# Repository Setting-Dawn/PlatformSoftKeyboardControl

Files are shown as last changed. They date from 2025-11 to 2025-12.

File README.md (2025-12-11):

#  PlatformSoftKeyboardControl 
Control a 2 Degree of Freedom Platform using a soft sensing sheet.

This README is also used as the main page for the Doxygen-generated documentation.
The remainder of this file contains project details, diagrams, and usage
information.
# PlatformSoftKeyboardControl 

Project Goal:

Control a 2 Degree of Freedom Platform using a custom piezoresistive sensing sheet.
## Mechanical Considerations
The balancing table is controlled by two motors connected to the table's surface via a strut with two ball joints that control rotation about perpendicular axes.

Lever Arm Powered By Motor

## Software Design
### Task Diagram

ESP32 Code Task Diagram

### Webserver Task 
The ESP32 hosts its own wifi on which it hosts a webpage on 192.168.5.1 that communicates the recorded data in csv forma to either the user or an external program that interprets it. The functionality of this task is based on an example by A. Sinha.

Webserver Task State Diagram

### Motor Control Task 
The motor control task awaits confirmation that the IMU has initialized and then begins operating the motor PIDs according to the setpoint stored in the xBar and yBar shares.

Motor Control State Diagram

### Material Reading Task 
In order to perform EIT analysis, a series of voltage differences needs to be measured. For one complete measurement, one electrode is grounded while its neighboring electrode is supplied with a current while the remaining electrodes are used to measure the voltage differences. This is then repeated for each electrode. This task is responsible for taking those individual datapoints and reporting the resulting 208 values to the webpage task to be published in csv format.

Material Reading State Diagram

### PyEIT interpretation
A python script using the pyEIT module is able to read the data hosted by the webpage and analyze any changes in resistivity of the material. The resulting centroid is then passed back to the webpage using url arguments.

## Other Code Used
- Liu, et al:
+ - https://github.com/eitcom/pyEIT 
- bryanduxbury:
+ - https://github.com/bryanduxbury/adc128d818_driver 
- yuskegoto:
+ - https://github.com/yuskegoto/PCA9956 
- spluttflob:
+ - PrintStream Library https://github.com/spluttflob/Arduino-PrintStream.git 
+ - ME507 Support Library https://github.com/spluttflob/ME507-Support.git
- madhephaestus:
+ - https://github.com/madhephaestus/ESP32Encoder

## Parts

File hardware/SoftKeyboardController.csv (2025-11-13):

Reference | Qty | Value | DNP | Exclude from BOM | Exclude from Board | Footprint | Datasheet
C1 | 1 | 470μF |  |  |  | Capacitor_THT:CP_Radial_D10.0mm_P5.00mm | ~
C2,C4,C5 | 3 | 0.1μF |  |  |  | Capacitor_SMD:C_0805_2012Metric | ~
C3 | 1 | 10μF |  |  |  | Capacitor_SMD:C_0805_2012Metric | ~
C6 | 1 | 2.2μF |  |  |  | Capacitor_SMD:C_0805_2012Metric | ~
ESP1 | 1 | NodeMCU |  |  |  | ME507F24:ESP32_NodeMCU_KeeYees
H1,H2,H3,H4 | 4 | MountingHole |  | Excluded from BOM |  | MountingHole:MountingHole_2.5mm | ~
IC1 | 1 | PCA9956BTWY |  |  |  | SOP50P640X110-39N | http://www.nxp.com/docs/en/data-sheet/PCA9956B.pdf
J1 | 1 | Barrel_Jack_Switch |  |  |  | Connector_BarrelJack:BarrelJack_CUI_PJ-102AH_Horizontal | ~
J2 | 1 | EXT IMU Connection |  |  |  | Connector_PinHeader_2.54mm:PinHeader_1x05_P2.54mm_Vertical | ~
J3 | 1 | Motor 1 |  |  |  | TerminalBlock_Phoenix:TerminalBlock_Phoenix_MKDS-1,5-2_1x02_P5.00mm_Horizontal | ~
J4 | 1 | Motor 2 |  |  |  | TerminalBlock_Phoenix:TerminalBlock_Phoenix_MKDS-1,5-2_1x02_P5.00mm_Horizontal | ~
J5,J6 | 2 | Conn_01x12_Socket |  |  |  | Connector_PinSocket_2.54mm:PinSocket_1x12_P2.54mm_Vertical | ~
J7,J8 | 2 | Conn_01x08_Socket |  |  |  | Connector_PinSocket_2.54mm:PinSocket_1x08_P2.54mm_Vertical | ~
J9 | 1 | Motor Encoder 2 |  |  |  | Connector_Molex:Molex_KK-396_A-41792-0005_1x05_P3.96mm_Horizontal | ~
J10 | 1 | Motor Encoder 1 |  |  |  | Connector_Molex:Molex_KK-396_A-41792-0005_1x05_P3.96mm_Horizontal | ~
R1,R5,R13 | 3 | 10kΩ |  |  |  | Resistor_SMD:R_0805_2012Metric | ~
R2,R6 | 2 | 4.7kΩ |  |  |  | Resistor_SMD:R_0805_2012Metric | ~
R3,R4 | 2 | 500mΩ |  |  |  | Resistor_SMD:R_0805_2012Metric | ~
R7 | 1 | 3.3kΩ |  |  |  | Resistor_SMD:R_0805_2012Metric | ~
R8,R9,R10,R11 | 4 | 470Ω |  |  |  | Resistor_SMD:R_0805_2012Metric | ~
R12 | 1 | 100 |  |  |  | Resistor_SMD:R_0805_2012Metric | ~
R14 | 1 | 1kΩ |  |  |  | Resistor_SMD:R_0805_2012Metric | ~
TP1,TP2,TP3,TP4,TP5,TP6,TP7,TP8,TP9,TP10,TP11 | 11 | TestPoint |  |  |  | TestPoint:TestPoint_Loop_D1.80mm_Drill1.0mm_Beaded | ~
U2,U3 | 2 | ADC128D818 |  |  |  | Package_SO:TSSOP-16_4.4x5mm_P0.65mm | http://www.ti.com/lit/ds/symlink/adc128d818.pdf
U4 | 1 | TL071 |  |  |  | Package_TO_SOT_SMD:SOT-23-5 | http://www.ti.com/lit/ds/symlink/tl071.pdf
U5 | 1 | CD74HC4067SM |  |  |  | Package_SO:SSOP-24_5.3x8.2mm_P0.65mm | http://www.ti.com/lit/ds/symlink/cd74hc4067.pdf
U6 | 1 | DRV8848 |  |  |  | Package_SO:TSSOP-16-1EP_4.4x5mm_P0.65mm | http://www.ti.com/lit/ds/symlink/drv8848.pdf

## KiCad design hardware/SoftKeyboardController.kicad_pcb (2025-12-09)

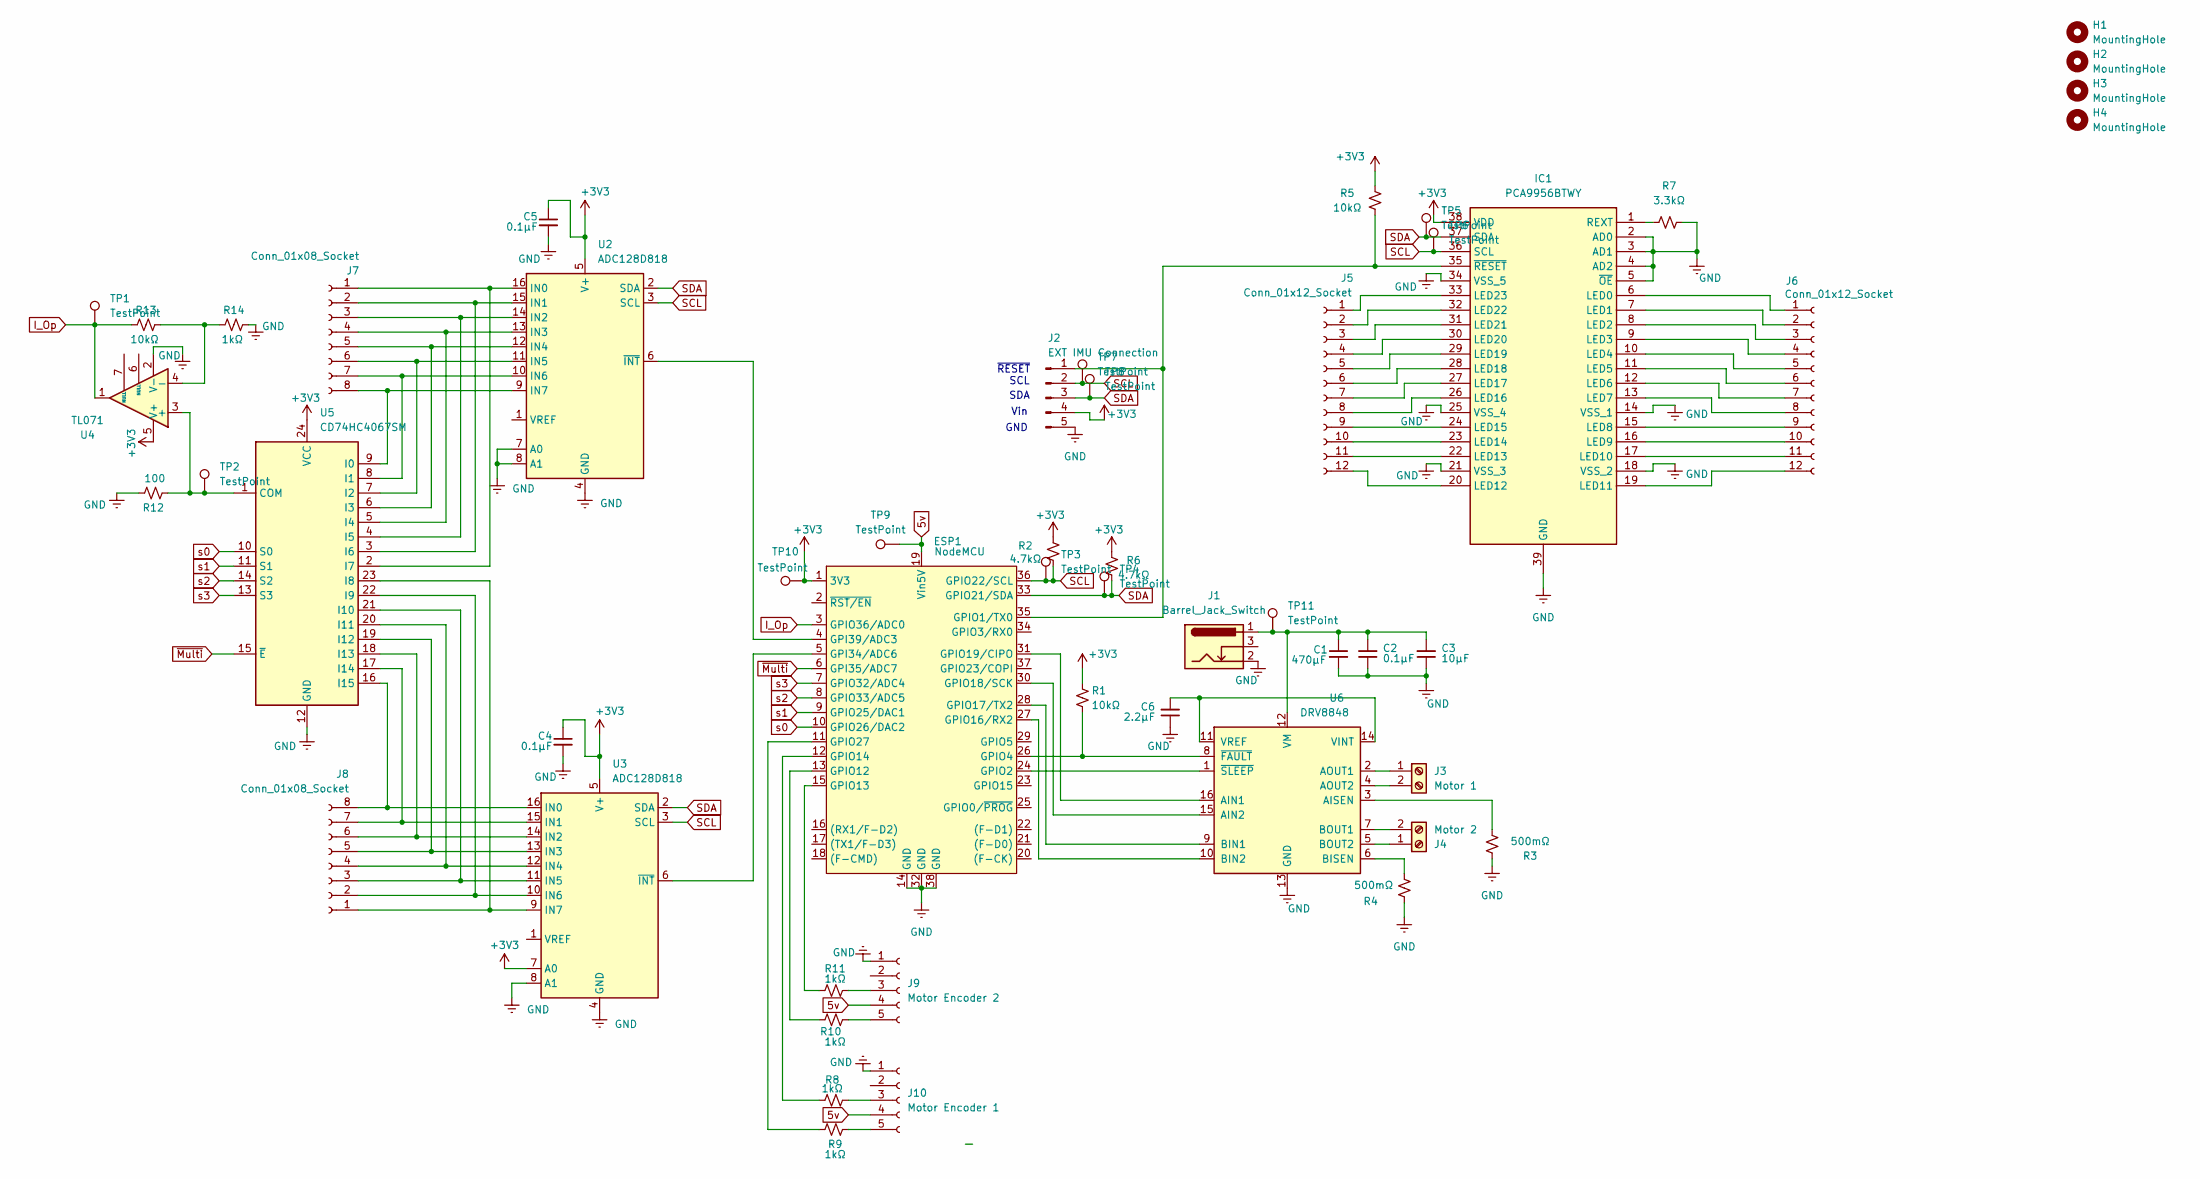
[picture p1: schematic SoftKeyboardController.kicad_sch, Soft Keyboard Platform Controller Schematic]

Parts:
C1: 470μF; CP_Radial_D10.0mm_P5.00mm
C2, C4, C5: 0.1μF; C_0805_2012Metric
C3: 10μF; C_0805_2012Metric
C6: 2.2μF; C_0805_2012Metric
ESP1: NodeMCU; ESP32_NodeMCU_KeeYees
H1, H2, H3, H4: MountingHole; MountingHole_2.5mm
IC1: PCA9956BTWY; SOP50P640X110-39N; Manufacturer_Part_Number PCA9956BTWY; Mouser Part Number 771-PCA9956BTWY
J1: Barrel_Jack_Switch; BarrelJack_CUI_PJ-102AH_Horizontal
J2: EXT IMU Connection; PinHeader_1x05_P2.54mm_Vertical
J3: Motor 1; TerminalBlock_Phoenix_MKDS-1,5-2_1x02_P5.00mm_Horizontal
J4: Motor 2; TerminalBlock_Phoenix_MKDS-1,5-2_1x02_P5.00mm_Horizontal
J5, J6: Conn_01x12_Socket; PinSocket_1x12_P2.54mm_Vertical
J7, J8: Conn_01x08_Socket; PinSocket_1x08_P2.54mm_Vertical
J9: Motor Encoder 2; Molex_KK-396_A-41792-0005_1x05_P3.96mm_Horizontal
J10: Motor Encoder 1; Molex_KK-396_A-41792-0005_1x05_P3.96mm_Horizontal
R1, R5, R13: 10kΩ; R_0805_2012Metric
R2, R6: 4.7kΩ; R_0805_2012Metric
R3, R4: 500mΩ; R_0805_2012Metric
R7: 3.3kΩ; R_0805_2012Metric
R8, R9, R10, R11, R14: 1kΩ; R_0805_2012Metric
R12: 100; R_0805_2012Metric
TP1, TP2, TP3, TP4, TP5, TP6, TP7, TP8, TP9, TP10, TP11: TestPoint; TestPoint_Loop_D1.80mm_Drill1.0mm_Beaded
U2, U3: ADC128D818; TSSOP-16_4.4x5mm_P0.65mm
U4: TL071; SOT-23-5
U5: CD74HC4067SM; SSOP-24_5.3x8.2mm_P0.65mm
U6: DRV8848; TSSOP-16-1EP_4.4x5mm_P0.65mm

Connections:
5v: ESP1.19 (Vin5V), J9.4, J10.4, TP9.1
+3V3: C4.1, C5.1, ESP1.1 (3V3), IC1.38 (VDD), J2.4, R1.1, R2.1, R5.1, R6.1, TP10.1, U2.5 (V+), U3.5 (V+), U3.7 (A0), U4.5 (V+), U5.24 (VCC)
GND: C1.2, C2.1, C3.1, C4.2, C5.2, C6.1, ESP1.14 (GND), ESP1.32 (GND), ESP1.38 (GND), IC1.2 (AD0), IC1.3 (AD1), IC1.4 (AD2), IC1.5 (~OE), IC1.14 (VSS_1), IC1.18 (VSS_2), IC1.21 (VSS_3), IC1.25 (VSS_4), IC1.34 (VSS_5), IC1.39 (GND), J1.2, J2.5, J9.1, J10.1, R3.1, R4.1, R7.1, R12.1, R14.1, U2.4 (GND), U2.7 (A0), U2.8 (A1), U3.4 (GND), U3.8 (A1), U4.2 (V-), U5.12 (GND), U6.13 (GND), U6.17 (GND)
I_Op: ESP1.3 (GPIO36/ADC0), R13.2, TP1.1, U4.1
unnamed: ESP1.5 (GPI34/ADC6), U3.6 (~INT)
unnamed: ESP1.4 (GPI39/ADC3), U2.6 (~INT)
unnamed: ESP1.35 (GPIO1/TX0), IC1.35 (~RESET), J2.1, R5.2
unnamed: ESP1.24 (GPIO2), U6.1 (~SLEEP)
unnamed: ESP1.26 (GPIO4), R1.2, U6.8 (~FAULT)
unnamed: ESP1.13 (GPIO12), R10.1
unnamed: ESP1.15 (GPIO13), R11.1
unnamed: ESP1.12 (GPIO14), R8.1
unnamed: ESP1.27 (GPIO16/RX2), U6.10 (BIN2)
unnamed: ESP1.28 (GPIO17/TX2), U6.9 (BIN1)
unnamed: ESP1.30 (GPIO18/SCK), U6.15 (AIN2)
unnamed: ESP1.31 (GPIO19/CIPO), U6.16 (AIN1)
unnamed: ESP1.11 (GPIO27), R9.1
unnamed: IC1.6 (LED0), J6.1
unnamed: IC1.7 (LED1), J6.2
unnamed: IC1.8 (LED2), J6.3
unnamed: IC1.9 (LED3), J6.4
unnamed: IC1.10 (LED4), J6.5
unnamed: IC1.11 (LED5), J6.6
unnamed: IC1.12 (LED6), J6.7
unnamed: IC1.13 (LED7), J6.8
unnamed: IC1.15 (LED8), J6.9
unnamed: IC1.16 (LED9), J6.10
unnamed: IC1.17 (LED10), J6.11
unnamed: IC1.19 (LED11), J6.12
unnamed: IC1.20 (LED12), J5.12
unnamed: IC1.22 (LED13), J5.11
unnamed: IC1.23 (LED14), J5.10
unnamed: IC1.24 (LED15), J5.9
unnamed: IC1.26 (LED16), J5.8
unnamed: IC1.27 (LED17), J5.7
unnamed: IC1.28 (LED18), J5.6
unnamed: IC1.29 (LED19), J5.5
unnamed: IC1.30 (LED20), J5.4
unnamed: IC1.31 (LED21), J5.3
unnamed: IC1.32 (LED22), J5.2
unnamed: IC1.33 (LED23), J5.1
unnamed: IC1.1 (REXT), R7.2
unnamed: J3.1, U6.2 (AOUT1)
unnamed: J3.2, U6.4 (AOUT2)
unnamed: J4.1, U6.5 (BOUT2)
unnamed: J4.2, U6.7 (BOUT1)
unnamed: J7.1, U2.16 (IN0), U5.2 (I7)
unnamed: J7.2, U2.15 (IN1), U5.3 (I6)
unnamed: J7.3, U2.14 (IN2), U5.4 (I5)
unnamed: J7.4, U2.13 (IN3), U5.5 (I4)
unnamed: J7.5, U2.12 (IN4), U5.6 (I3)
unnamed: J7.6, U2.11 (IN5), U5.7 (I2)
unnamed: J7.7, U2.10 (IN6), U5.8 (I1)
unnamed: J7.8, U2.9 (IN7), U5.9 (I0)
unnamed: J8.1, U3.9 (IN7), U5.23 (I8)
unnamed: J8.2, U3.10 (IN6), U5.22 (I9)
unnamed: J8.3, U3.11 (IN5), U5.21 (I10)
unnamed: J8.4, U3.12 (IN4), U5.20 (I11)
unnamed: J8.5, U3.13 (IN3), U5.19 (I12)
unnamed: J8.6, U3.14 (IN2), U5.18 (I13)
unnamed: J8.7, U3.15 (IN1), U5.17 (I14)
unnamed: J8.8, U3.16 (IN0), U5.16 (I15)
unnamed: J9.3, R11.2
unnamed: J9.5, R10.2
unnamed: J10.3, R8.2
unnamed: J10.5, R9.2
unnamed: R12.2, TP2.1, U4.3 (+), U5.1 (COM)
unnamed: R13.1, R14.2, U4.4 (-)
unnamed: R3.2, U6.3 (AISEN)
unnamed: R4.2, U6.6 (BISEN)
unnamed: C6.2, U6.11 (VREF), U6.14 (VINT)
unnamed: C1.1, C2.2, C3.2, J1.1, TP11.1, U6.12 (VM)
SCL: ESP1.36 (GPIO22/SCL), IC1.36 (SCL), J2.2, R2.2, TP3.1, TP6.1, TP7.1, U2.3 (SCL), U3.3 (SCL)
SDA: ESP1.33 (GPIO21/SDA), IC1.37 (SDA), J2.3, R6.2, TP4.1, TP5.1, TP8.1, U2.2 (SDA), U3.2 (SDA)
s0: ESP1.10 (GPIO26/DAC2), U5.10 (S0)
s1: ESP1.9 (GPIO25/DAC1), U5.11 (S1)
s2: ESP1.8 (GPIO33/ADC5), U5.14 (S2)
s3: ESP1.7 (GPIO32/ADC4), U5.13 (S3)
~Multi: ESP1.6 (GPI35/ADC7), U5.15 (~E)

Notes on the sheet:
GND
~{RESET}
Vin
SDA
SCL

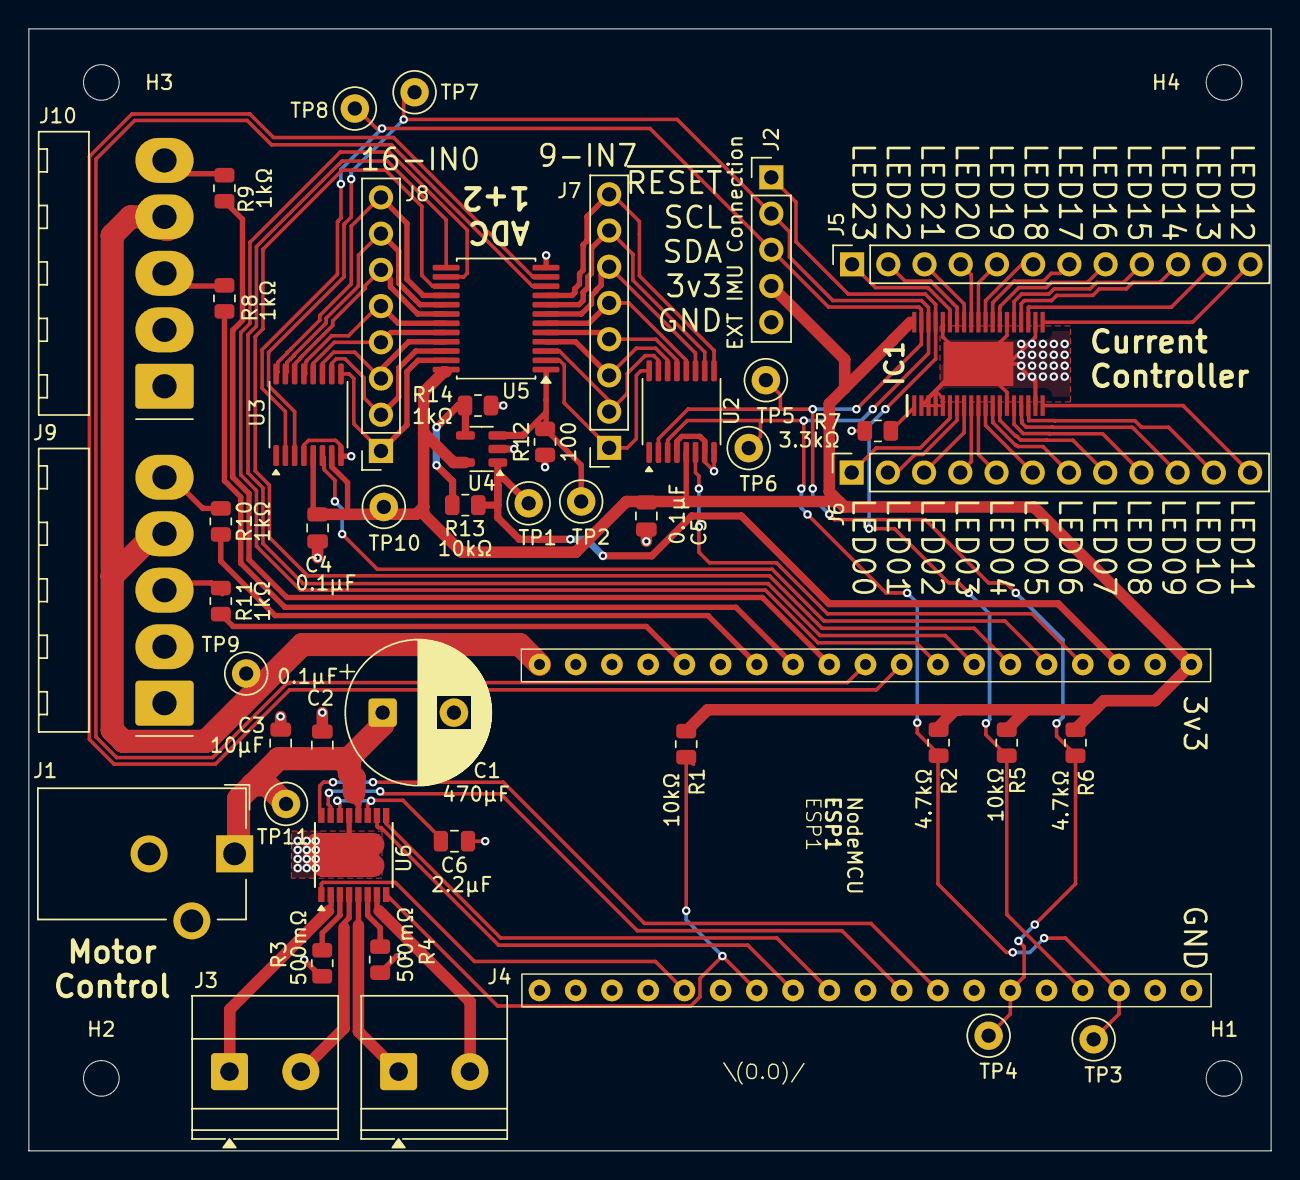
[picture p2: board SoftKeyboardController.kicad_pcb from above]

Board: 2 copper layers, 87.1 x 78.7 mm, 52 parts (0 on the bottom side), 79 nets.

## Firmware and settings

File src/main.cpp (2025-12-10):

/*! @file main.cpp
*   @brief This project was created to run the soft-sensor activated balancing platform
*   as the final project of Cal Poly SLO Fall ME 507 class.
*   @author Setting-Dawn
*   @author Jake Rowen
*   @author Ethan Siahpush
*   @version 2.0.0
*   @date 2025-Dec-09
*/

#include <Arduino.h>
#include <ESP32Encoder.h>
#include <Wire.h>
#include <Adafruit_Sensor.h>
#include <Adafruit_BNO055.h>
#include <cmath>
#include <WebServer.h>

#include "ADC128D818.h"
#include "PCA9956.h"
#include "PrintStream.h"

#include "IMU.h"
#include "MOTOR.h"
#include "ENCODER.h"
#include "EITwebhost.h"
#include "CD74HC4067SM.h"
#include "shares.h"

#undef DEBUG_MOTOR
#undef DEBUG_READMATERIAL
#undef DEBUG_ALL
#undef DEBUG_WEB
#undef SCANTWI

#ifdef DEBUG_ALL
#define DEBUG_MOTOR
#define DEBUG_READMATERIAL
#define DEBUG_WEB
#endif

// Multiplexer control pins
const uint8_t s0_PIN = 26;
const uint8_t s1_PIN = 25;
const uint8_t s2_PIN = 33;
const uint8_t s3_PIN = 32;
const uint8_t MultiEnable_PIN = 35;

// ADC TWI Addresses
const uint8_t ADC_1ADDRESS = 0x1D;
const uint8_t ADC_2ADDRESS = 0x1F;

// PCA9956BTWY Address
const uint8_t PCA9956_ADDRESS = 0x01;
PCA9956 CurrCtrl (&Wire);

// Pin definition for motors
uint8_t nSleepPin = 02;

uint8_t motorXPin1 = 19;
uint8_t motorXPin2 = 18;

uint8_t motorYPin1 = 17;
uint8_t motorYPin2 = 16;
ESP32Encoder encoderX;
ESP32Encoder encoderY;

// A share which holds whether the external program needs to initialize
Share<bool> initializeVFLG ("Measure V0");
// A share which holds whether the external program should read voltages
Share<bool> readVFLG ("Read V");
// Shares to communicate target position between webpage and motor control tasks
Share<float> xBar ("X Centroid");
Share<float> yBar ("Y Centroid");
// A share which holds the data to be published
float publish[208] = {0};
Share<bool> dataAvailable ("Publish Flag");
// Mutex to thread protect the
SemaphoreHandle_t twiMutex;

/*!
* @brief Task to handle cycling through the pins to take EIT voltage readings
* @details First waits for initialization of twi communication to complete.
* Then each round has one channel with an applied current, one grounded, and 14 others.
* ADCs read all adc channels, discards the two non-read channels, finds the deltaV between appropriate pins
* and stores all values in the resulting array into a global array after lowering the dataAvailable flag.
* @param p_params void*, unused.
*/
void task_ReadMaterial(void* p_params) {
    Serial << "Starting Read Material Task" << endl;
    ADC128D818 ADC_1 (ADC_1ADDRESS);
    ADC128D818 ADC_2 (ADC_2ADDRESS);
    CD74HC4067SM Multiplex (s0_PIN,s1_PIN,s2_PIN,s3_PIN,MultiEnable_PIN);
    PCA9956 CurrCtrl (&Wire);

    const uint8_t maxCurrent = 0xFF;

    uint8_t currPinIndex;
    double measure[208] = {0}; // Somewhere to store the data for 1 complete measurement
    double cycleVals[16]; // Somewhere to store the data for 1 energization state
    double skipCycleVals[14]; // Somewhere to store the important data begining at the correct index for 1 energization state
    Serial << "Finished initializing Read Material Task" << endl;

    uint8_t cycleIndex = 0;
    uint8_t state = 0; // Initialization State

    for (;;) {
        #ifdef DEBUG_READMATERIAL
        Serial << "Material Task " << state << endl;
        #endif
        // Operation requires the TWI devices be initialized, but other tasks include other twi devices.
        // Priority for this isn't important, so it will just sit in this state until able to initialize.
        if (state == 0) // Start TWI communication
        {
            if (xSemaphoreTake(twiMutex,5) == pdTRUE) // Takes the mutex and returns true if successful
            {
                ADC_1.setOperationMode(SINGLE_ENDED); //Mode 1 reads voltages on channels 0-7
                ADC_1.begin(); // Initializes ADC1
                ADC_2.setOperationMode(SINGLE_ENDED);//Mode 1 reads voltages on channels 0-7
                ADC_2.begin(); // Initializes ADC2
                CurrCtrl.init(PCA9956_ADDRESS,0xFF,false); // Initialize current control address and max brightnes
                xSemaphoreGive(twiMutex); // Use of twi is complete, free mutex
                state = 1; // Switch to reading the material
            }
        }

        else if (state == 1) // Change Energization State
        {
            // cycleIndex initializes to n=0, which is also the grounded electrode.
            currPinIndex = (cycleIndex + 1) % 16; // The electrode with current applied is always n+1
            
            // Attempt to send TWI instruction to change LED
            if (xSemaphoreTake(twiMutex,5) == pdTRUE) // Takes the mutex and returns true if successful
            {
                CurrCtrl.offLED(cycleIndex); // Stop producing current for what will become the grounded pin
                Multiplex.switchPin(cycleIndex); // Use multiplexer to ground the appropriate pin
                CurrCtrl.onLED(currPinIndex); // Start producing current on the appropriate pin
                xSemaphoreGive(twiMutex); // Use of twi is complete, free mutex
                state = 2; // Only advances to start recording if communication was successful
            }
        }
        
        // After a short delay, try to take all the available measurements for 1 energization state
        else if (state == 2) 
        {
            if (xSemaphoreTake(twiMutex,5) == pdTRUE) // Takes the mutex and returns true if successful
            {
                // Record all ADC channels, electrodes 0-15 are recorded in order by ADC1 7-0 and then ADC2 7-0
                for (uint8_t i=0;i<8;i++) {
                    cycleVals[i] = ADC_1.readConverted(7-i);
                    cycleVals[8+i] = ADC_2.readConverted(7-i);

                    #ifdef DEBUG_READMATERIAL
                    Serial << cycleVals[i] << endl;
                    Serial << cycleVals[8+i] << endl;
                    #endif

                };
                Serial << "Finished a full round, giving Mutex" << endl;
                xSemaphoreGive(twiMutex); // Use of twi is complete, free mutex
                Serial << "Finished a full round and Gave Mutex" << endl;
                
                // Grounded pin and current pin are not used in analysis so the 0th measurement
                // should be grounded pin +2 or current pin + 1.
                for (uint8_t i=0;i<14;i++) 
                {
                    skipCycleVals[i] = cycleVals[(currPinIndex + 1 + i) % 16];
                    #ifdef DEBUG_READMATERIAL
                    Serial << skipCycleVals[i] << endl;
                    #endif
                };
                Serial << "end skip" << endl;

                // Finds all the deltaV values used and stores them in a local data storage array,
                // ordered according to which of the 16 energization states is being recorded.
                for (uint8_t i=0;i<13;i++) 
                {
                    measure[cycleIndex*13+i] = skipCycleVals[i+1] - skipCycleVals[i];
                };

                cycleIndex++; // Advances to the next energization state.
                if (cycleIndex == 16)
                {
                    Serial << "Finished a full measurement" << endl;
                    cycleIndex = 0; // Resets energization marker to ground pin n=0
                    state = 3; // Change to publish value state
                }
                else
                {
                    state = 1;
                }
            }
        }

        // Pushes all locally stored measurements to a global array accessable by the webpage task
        else if (state == 3) 
        {
            #ifdef DEBUG_READMATERIAL
            Serial << "publishing values" << endl;
            Serial << dataAvailable.get() << endl;
            #endif
            if (dataAvailable.get()) // Checks if the webpage task is currently attempting to read values
            {
                dataAvailable.put(false); // Lower the flag to avoid corrupted data
                #ifdef DEBUG_READMATERIAL
                Serial << "Took dataMutex" << endl;
                #endif
                // Record every datapoint
                for (uint8_t n=0;n<208;n++) 
                {
                    publish[n] = measure[n];
                    #ifdef DEBUG_READMATERIAL
                    Serial << measure[n] << endl;
                    #endif
                }
                dataAvailable.put(true); // data is no longer being used, raise the allow flag
                if (readVFLG.get() == false) {
                    if (initializeVFLG.get() == false)
                    {
                        initializeVFLG.put(true);
                    }
                    else
                    {
                        readVFLG.put(true);
                    }
                }
                #ifdef DEBUG_READMATERIAL
                Serial << "Gave dataMutex" << endl;
                #endif
                state = 1; // go back to energizing the newest state
            }
            else {
                Serial << "Failed to take dataMutex" << endl;
            }
        }
        vTaskDelay(50/portTICK_PERIOD_MS); // Delay 50ms
    }
}

/*!
* @brief Task to handle controlling the table position using an IMU and two motors
* @details Has PID control on both motors to attempt to reach the desired setpoint and measured by a BNO055A IMU.
* @param p_params void*, unused.
*/
void task_controlMotors(void *parameter) {
    float x_angle, y_angle, xTargetAngle, yTargetAngle, xAngleErr, yAngleErr, errSumX,errSumY, effX, effY;
    float xAngleErrOld,yAngleErrOld;
    int16_t encoderXTicks, encoderYTicks, errX, errY;
    uint8_t pwm_X, pwm_Y;
    const float KP = 40; // Proportional gain for speed control
    const float KI = 0.1; // Integral gain for speed control
    const float KD = 10; // Integral gain for speed control
    
    uint8_t maxAngle = 10; // software limit for desired angle
    xTargetAngle = 0.0; // Target angle is 0 degrees by default
    yTargetAngle = 0.0; // Target angle is 0 degrees by default
    
    MOTOR_brake(motorXPin1, motorXPin2, 0, 1); // Initially stop both motors
    MOTOR_brake(motorYPin1, motorYPin2, 2, 3);

    uint8_t state = 0;
    for (;;) {
        // Initial State waits for IMU to initialize
        if (state == 0) {
            if (xSemaphoreTake(twiMutex,5) == pdTRUE) // Takes the mutex and returns true if successful
            {
                // Only advance states if IMU sucessfully initializes
                if (!IMU_init(5)) {
                    Serial.println("Failed to initialize IMU!");
                }
                else {
                    Serial.println("IMU initialized.");
                    state = 1;
                }
                xSemaphoreGive(twiMutex);
            }
        }
        // After Initialization, control the motor according to setpoint
        else if (state == 1) {
            /* get the currentl angles of the platform*/
            if (xSemaphoreTake(twiMutex,5) == pdTRUE) 
            {
                IMU_getAngles(x_angle, y_angle);
                xSemaphoreGive(twiMutex);
            }
            // if (abs(x_angle) > 15.0f || abs(y_angle) > 15.0f) {
            //     // If tilt angle exceeds 15 degrees, stop motors for safety
            //     MOTOR_brake(motorXPin1, motorXPin2, 0, 1);
            //     MOTOR_brake(motorYPin1, motorYPin2, 2, 3);
            //     Serial.println("Tilt angle too high! Motors stopped for safety.");
            //     vTaskDelay(500 / portTICK_PERIOD_MS);  // Delay for 500 ms
            //     continue; // Skip the rest of the loop
            // }

            // Adopts targets communicated by the webpage task
            xTargetAngle = xBar.get()*maxAngle; // Centroid values communicated are from -1 to 1
            yTargetAngle = yBar.get()*maxAngle;

            // Determine error
            xAngleErr = xTargetAngle - x_angle;
            yAngleErr = yTargetAngle - y_angle;
            
            // Constrain Integral Error to produce at most max effort to eliminate run-away integral control
            errSumX = constrain(errSumX + xAngleErr,-2550,2550);
            errSumY = constrain(errSumY + yAngleErr,-2550,2550);
            #ifdef DEBUG
            Serial << endl;
            Serial << xAngleErr << " " << yAngleErr << endl;
            Serial << errSumX << " " << errSumY << endl;
            #endif
            // Calculate appropriate effort
            effX = xAngleErr*KP + errSumX*KI + (xAngleErr-xAngleErrOld)*KD;
            effY = yAngleErr*KP + errSumY*KI + (yAngleErr-yAngleErrOld)*KD;
            
            // Assign previous error for use in derivative control
            xAngleErrOld = xAngleErr;
            yAngleErrOld = yAngleErr;

            // constrain effort to maximum allowed
            pwm_X = constrain((abs(effX)), 0, 255);
            pwm_Y = constrain((abs(effY)), 0, 255);
            
            #ifdef DEBUG
            Serial.print(pwm_X);
            Serial.print(" ");
            Serial.println(pwm_Y);
            #endif

            /* control motor X*/
            if (effX > 0) {
                MOTOR_forward(motorXPin1, motorXPin2, 0, 1, pwm_X);
            } else if (effX < 0) {
                MOTOR_reverse(motorXPin1, motorXPin2, 0, 1, pwm_X);
            } else {
                MOTOR_brake(motorXPin1, motorXPin2, 0, 1); // Shouldn't get here
            }
            /* control motor Y*/
            if (effY > 0) {
                MOTOR_reverse(motorYPin1, motorYPin2, 2, 3, pwm_Y);
            } else if (effY < 0) {
                MOTOR_forward(motorYPin1, motorYPin2, 2, 3, pwm_Y);
            } else {
                MOTOR_brake(motorYPin1, motorYPin2, 2, 3); // Shouldn't get here
            }
        }
        vTaskDelay(5/portTICK_PERIOD_MS); // Delay for 5 ms
    }
}

/*!
* @brief Task to handle the webpage for user interfacing.
* @details publishes all 208 datapoints used for 1 measurement and some flags used by an external python program
* to know whether to initialize a base value or make appropriate calculations. Additionally, uses args on the webpage
* to allow the user or external python program to set a desired table position.
* @param p_params void*, unused.
*/
void task_webserver (void* p_params)
{
    #ifdef DEBUG_WEB
    Serial << "handling Webpage" << endl;
    #endif
    // The server has been created statically when the program was started and
    // is accessed as a global object because not only this function but also
    // the page handling functions referenced below need access to the server
    server.on ("/", handle_DocumentRoot);
    server.on ("/data", handle_data);
    server.on ("/set", handleSetValues);
    server.on ("/flags", handleFlags);
    server.onNotFound (handle_NotFound);

    // Get the web server running
    server.begin ();
    Serial.println ("HTTP server started");

    // Task only has a single state, but changes behavior based on web requests as show above.
    for (;;)
    {
        // The web server must be periodically run to watch for page requests
        server.handleClient ();
        vTaskDelay (100/portTICK_PERIOD_MS); //delay 100 ms
    }
}

#ifndef SCANTWI
void setup() {
    Serial.begin(115200);
    delay(1000);

    twiMutex = xSemaphoreCreateMutex();

    /* Initialize motors  */
    MOTOR_init(motorXPin1, motorXPin2, 0, 1);
    MOTOR_init(motorYPin1, motorYPin2, 2, 3);

    /* initialize encoders*/
    ENCODER_init(encoderX, 27, 14);
    ENCODER_init(encoderY, 12, 13);

    pinMode(nSleepPin, OUTPUT);
    digitalWrite(nSleepPin, HIGH); // Wake up motor driver

    // Assign default share values
    initializeVFLG.put(false);
    readVFLG.put(false);
    xBar.put(0.0);
    yBar.put(0.0);
    dataAvailable.put(true);

    // Call function which gets the WiFi working
    setup_wifi();

    Serial.println("Setup complete.");

    /* Create control task */
    xTaskCreate(
         task_controlMotors,   // Task function
         "Control Motors",     // Name of the task
         4096,                 // Stack size (in words)
         NULL,                 // Task input parameter
         1,                    // Priority of the task
         NULL                 // Task handle
     );
    
    // Task which produces the blinking LED
    xTaskCreate (task_ReadMaterial, "EIT Read", 65536, NULL, 7, NULL);

    // Task which runs the web server.
    xTaskCreate (task_webserver, "Web Server", 8192, NULL, 3, NULL);
}

void loop() {
    vTaskDelay(portMAX_DELAY); //Don't need to run the default loop.
}

#else 
uint8_t readRegister(uint8_t reg) {
  Wire.beginTransmission(PCA9956_ADDRESS);
  Wire.write(reg);
  if (Wire.endTransmission(false) != 0) {  // repeated start
    return 0xFF; // error marker
  }

  if (Wire.requestFrom(PCA9956_ADDRESS, (uint8_t)1) != 1) {
    return 0xFF; // error
  }
  return Wire.read();
}

void setup() {
  Serial.begin(115200);
  Wire.begin(21, 22);  // or your SDA/SCL

  delay(100);

  // Step 1: ping
  Wire.beginTransmission(PCA9956_ADDRESS);
  uint8_t err = Wire.endTransmission();
  
PCA9956 CurrCtrl (&Wire);

const uint8_t maxCurrent = 0xFF;
CurrCtrl.init(PCA9956_ADDRESS,maxCurrent,false);

if (err != 0) {
Serial.print("No ACK at 0x01, error = ");
Serial.println(err);
return;
}

Serial.println("ACK from 0x01, attempting to read MODE1...");
CurrCtrl.onLED(0);

  // Step 2: read MODE1 (reg 0x00)
}

void loop() {
  vTaskDelay(30000);
//   uint8_t count = 0;

//   Serial.println("Scanning...");

//   for (uint8_t address = 1; address < 127; address++) {
//     Wire.beginTransmission(address);
//     uint8_t error = Wire.endTransmission();

//     if (error == 0) {
//       Serial.print("TWI device found at 0x");
//       if (address < 16) Serial.print("0");
//       Serial.println(address, HEX);
//       count++;
//     }
//   }

//   if (count == 0) {
//     Serial.println("No TWI devices found");
//   }

//   Serial.println("Done.\n");
//   delay(2000);
}
#endif

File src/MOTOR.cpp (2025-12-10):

/** Implementation of motor commands */

#include "MOTOR.h"
#include <Arduino.h>

/**
 * @file MOTOR.cpp
 * @brief Initialize motor control pins and PWM channels.
 * 
 * Configures the specified GPIO pins for motor output and sets up
 * two independent PWM channels at 25 kHz with 8-bit resolution.
 * 
 * @param pin1 GPIO pin for motor direction 1
 * @param pin2 GPIO pin for motor direction 2
 * @param channel1 PWM channel number for first direction (0-15)
 * @param channel2 PWM channel number for second direction (0-15)
 * 
 * @return void
 * 
 * @details Both PWM channels are configured with:
 *   - Frequency: 25 kHz
 *   - Resolution: 8-bit (0-255)
 *   - Duty cycle controlled via ledcWrite()
 */
void MOTOR_init(uint8_t pin1,uint8_t pin2, uint8_t channel1, uint8_t channel2) {
    pinMode(pin1, OUTPUT);
    pinMode(pin2, OUTPUT);
    ledcSetup(channel1, 25000, 8);
    ledcSetup(channel2, 25000, 8);
    ledcAttachPin(pin1, channel1);
    ledcAttachPin(pin2, channel2);
}
    
/**
 * @brief Drive the motor forward at a specified speed.
 * 
 * Applies forward motion by writing the speed value to the forward channel
 * and setting the reverse channel to 0. The motor will move in the forward
 * direction proportional to the speed parameter.
 * 
 * @param pin1 GPIO pin for motor direction 1 (unused in this implementation)
 * @param pin2 GPIO pin for motor direction 2 (unused in this implementation)
 * @param channel1 PWM channel for forward motion
 * @param channel2 PWM channel for reverse motion
 * @param speed PWM duty cycle (0-255, where 255 is maximum speed)
 * 
 * @return void
 * 
 * @note To change direction, call MOTOR_reverse() or MOTOR_brake()
 * 
 * @see MOTOR_reverse(), MOTOR_brake()
 */
void MOTOR_forward(uint8_t pin1,uint8_t pin2, uint8_t channel1, uint8_t channel2, uint8_t speed) {
    ledcWrite(channel1, speed);
    ledcWrite(channel2, 0);
}

/**
 * @brief Drive the motor in reverse at a specified speed.
 * 
 * Applies reverse motion by writing the speed value to the reverse channel
 * and setting the forward channel to 0. The motor will move in the reverse
 * direction proportional to the speed parameter.
 * 
 * @param pin1 GPIO pin for motor direction 1 (unused in this implementation)
 * @param pin2 GPIO pin for motor direction 2 (unused in this implementation)
 * @param channel1 PWM channel for forward motion
 * @param channel2 PWM channel for reverse motion
 * @param speed PWM duty cycle (0-255, where 255 is maximum speed)
 * 
 * @return void
 * 
 * @note To change direction, call MOTOR_forward() or MOTOR_brake()
 * 
 * @see MOTOR_forward(), MOTOR_brake()
 */
void MOTOR_reverse(uint8_t pin1,uint8_t pin2, uint8_t channel1, uint8_t channel2, uint8_t speed) {
    ledcWrite(channel1, 0);
    ledcWrite(channel2, speed);
}

/**
 * @brief Apply electrical braking to stop the motor quickly.
 * 
 * Applies maximum PWM signal to both motor channels simultaneously, causing
 * them to work against each other and bring the motor to a rapid stop through
 * electrical braking. This is more effective than coasting to a stop.
 * 
 * @param pin1 GPIO pin for motor direction 1 (unused in this implementation)
 * @param pin2 GPIO pin for motor direction 2 (unused in this implementation)
 * @param channel1 PWM channel for forward motion
 * @param channel2 PWM channel for reverse motion
 * 
 * @return void
 * 
 * @details Both channels are set to 255 (maximum duty cycle), creating
 * opposing forces that provide rapid deceleration.
 * 
 * @see MOTOR_forward(), MOTOR_reverse()
 */
void MOTOR_brake(uint8_t pin1,uint8_t pin2, uint8_t channel1, uint8_t channel2) {
    ledcWrite(channel1, 255);
    ledcWrite(channel2, 255);
}

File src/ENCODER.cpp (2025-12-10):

/*! 
 * @file ENCODER.cpp
 * @brief Implementation file for encoder helper functions.
 * @details Provides initialization and simple helper wrappers for the
 *          ESP32Encoder objects used by the project.
 */
#include "ENCODER.h"

/**
 * @brief Initialize an encoder with full quadrature decoding.
 * 
 * Configures the ESP32 encoder to use internal weak pull-up resistors and
 * attaches it to the specified pins for full quadrature counting. If inverted
 * flag is set, the encoder count direction is reversed.
 * 
 * @param encoder Reference to the ESP32Encoder object to initialize
 * @param pinA First GPIO pin for encoder input (typically Phase A)
 * @param pinB Second GPIO pin for encoder input (typically Phase B)
 * @param inverted Boolean flag to reverse the count direction:
 *                 true = negate the current count for inverted direction
 *                 false = use normal counting direction
 * 
 * @return void
 * 
 * @details Enables ESP32Encoder internal weak pull-up resistors and uses
 * full quadrature decoding for 4x count resolution.
 * 
 * @see ENCODER_getCount(), ENCODER_zero()
 */
void ENCODER_init(ESP32Encoder &encoder, uint8_t pinA, uint8_t pinB, bool inverted) {
    ESP32Encoder::useInternalWeakPullResistors = puType ::up;
    encoder.attachFullQuad(pinA, pinB);
    if (inverted) {
        encoder.setCount(-encoder.getCount());
    }
}

/**
 * @brief Retrieve the current encoder count value.
 * 
 * Returns the current count from the ESP32 encoder. The count represents
 * the accumulated encoder position and may be positive or negative depending
 * on the direction of rotation and whether the encoder was inverted.
 * 
 * @param encoder Reference to the ESP32Encoder object to read from
 * 
 * @return int64_t The current encoder count value
 * 
 * @details This function reads the counter without modifying its state.
 * For full quadrature decoding, each mechanical detent may count as multiple
 * counts depending on the encoder type (typically 4 counts per detent).
 * 
 * @see ENCODER_init(), ENCODER_zero()
 */
int64_t ENCODER_getCount(ESP32Encoder &encoder) {
    return encoder.getCount();
}

/**
 * @brief Reset the encoder count to zero.
 * 
 * Sets the encoder's internal counter to 0, allowing measurement of displacement
 * from this new reference point. This is useful for tracking relative motion
 * or establishing a home position.
 * 
 * @param encoder Reference to the ESP32Encoder object to reset
 * 
 * @return void
 * 
 * @see ENCODER_init(), ENCODER_getCount()
 */
void ENCODER_zero(ESP32Encoder &encoder) {
    encoder.setCount(0);
}

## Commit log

2025-10-17 v1.0 Schematic
    [SoftKeyboardController.kicad_sch]
2025-10-17 Update Schematic to v1.1 (redo of pull request)
    [SoftKeyboardController.kicad_sch]
2025-10-24 ADC chips
    [SoftKeyboardController.kicad_sch]
2025-10-24 Added Transistors & ADCs to schematic. V1 of PCB
    [SoftKeyboardController.kicad_pcb, temp.kicad_sch]
2025-10-24 Delete SoftKeyboardController/temp.kicad_sch
    Removed temp files created during backup recovery
    [temp.kicad_sch]
2025-10-30 Shrink Footprint
    Relocated and re-traced board to improve overall footprint
    [SoftKeyboardController.kicad_pcb, SoftKeyboardController.kicad_sch]
2025-10-30 Added motor encoder connections
    [SoftKeyboardController.kicad_sch]
2025-11-07 Remapped Board again
    Version of Board before ordering
    [SoftKeyboardController-B_Cu.gbl, SoftKeyboardController-B_Cu.gbr, SoftKeyboardController-B_Mask.gbr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]
2025-11-08 changed capacitor footprint to reflect actual capacitor
    [SoftKeyboardController-B_Cu.gbl, SoftKeyboardController-B_Mask.gbs, SoftKeyboardController-B_Paste.gbp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]
2025-11-09 re ran gerber file export
    [SoftKeyboardController-B_Cu.gbl, SoftKeyboardController-B_Cu.gbr, SoftKeyboardController-B_Mask.gbr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]
2025-11-09 updated zip file with gerber files
2025-11-13 remove errored lock file
    [SoftKeyboardController.csv]
2025-11-14 rename hardware folder for clarity
    [SoftKeyboardController-B_Cu.gbl, SoftKeyboardController-B_Mask.gbs, SoftKeyboardController-B_Paste.gbp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]
2025-12-09 Final Version of Code
    Compiled motor control code with material reading code
2025-12-09 small change to board reflecting fixed SCL and SDA miswiring
    [SoftKeyboardController.kicad_pcb, SoftKeyboardController.kicad_sch]
2025-12-10 Add doxygen files
    [SoftKeyboardController.kicad_sch]
2025-12-11 it works! attach README correctly in doxygen
